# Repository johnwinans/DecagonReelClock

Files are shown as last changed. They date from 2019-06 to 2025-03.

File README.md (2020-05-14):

# DecagonReelClock
Design files for a 3D printed decagon reel clock.  Project files include a 2-part 
decagon reel, drive gear, mounting bracket and printable digits to glue onto the reels.

Inspired by various pinball counter and clock projects like this one:

https://makezine.com/projects/convert-pinball-score-reel-clock/

...and the Gottlieb Decagon Score Reels of the '70s:

https://youtu.be/1tYzWID41jc

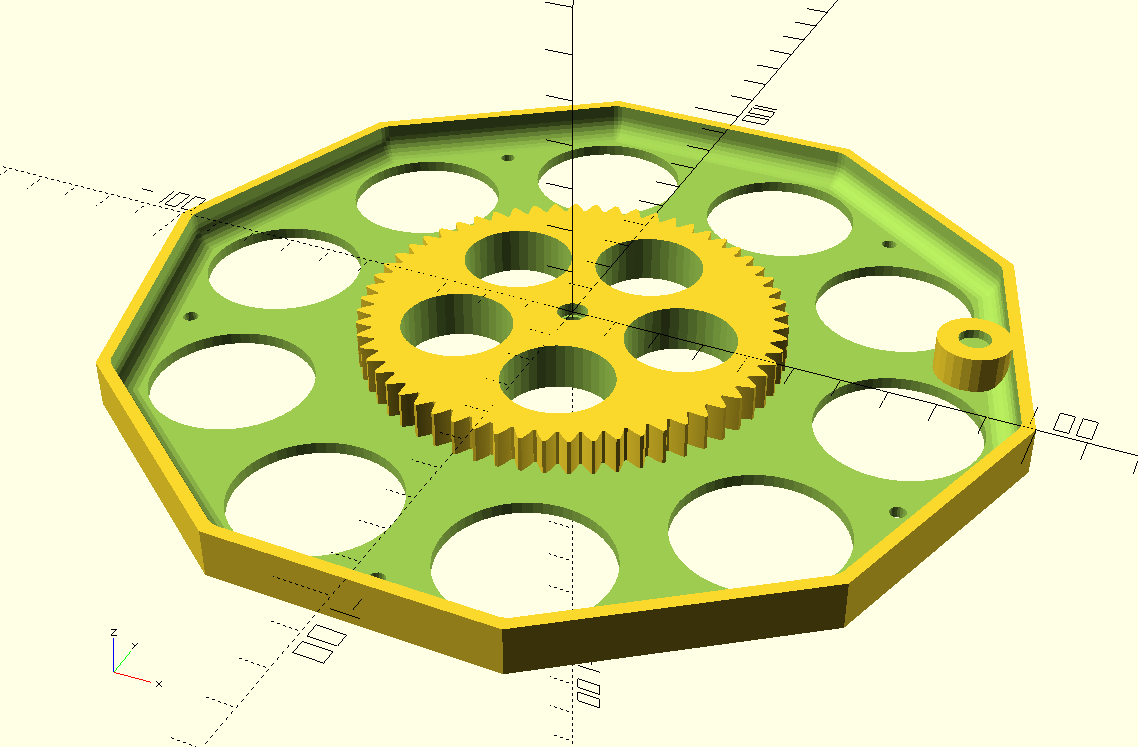
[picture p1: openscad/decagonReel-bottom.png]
Decagon Back


Part suppliers:

* NEMA 17 stepper motors (for 200mm reels) amazon.com ASIN: B07582D2R8
* 28BYJ-48 stepper motors (for 140mm reels) amazon.com ASIN: B00LPK0E5A
* 3mm x 150mm axles amazon.com ASIN: B00JR56KI0
* 3mm bearings amazon.com ASIN: B00ZHSQX42
* Index magnets amazon.com ASIN: B07CPMQJHF
* M3 bolts: asmc.net 0000-102370
* M3 NYLOC nuts: asmc.net 0000-102035
* M3 grub screws amazon.com ASIN: B07792FFJV
* M3 washers amazon.com ASIN: B000FN15YM

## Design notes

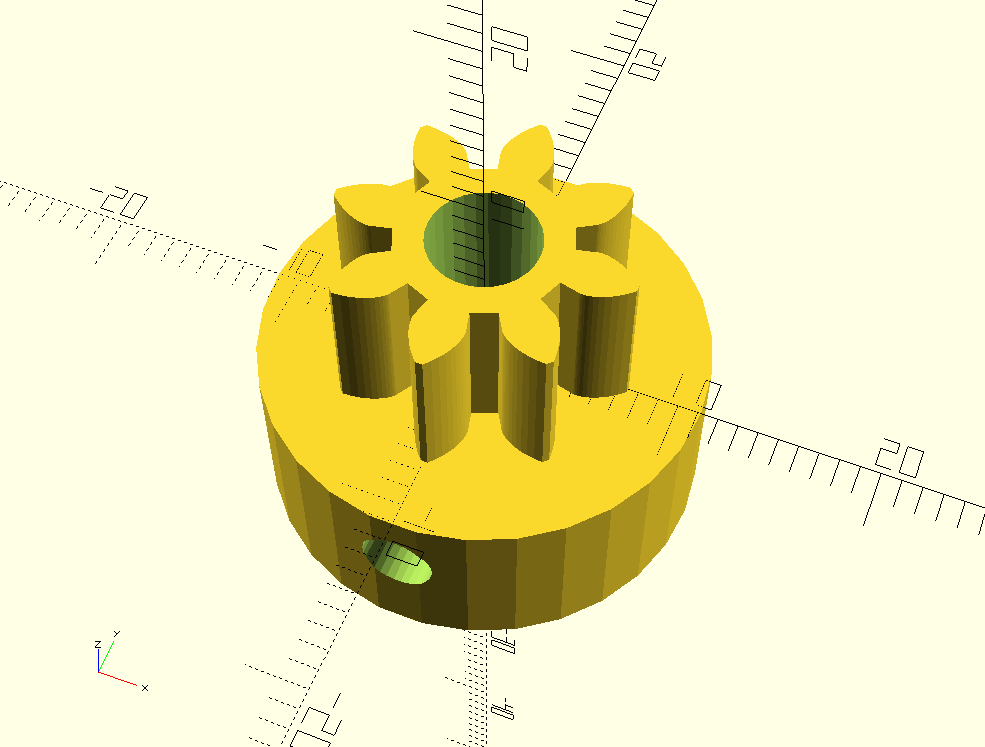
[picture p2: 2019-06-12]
openscad/gear.png

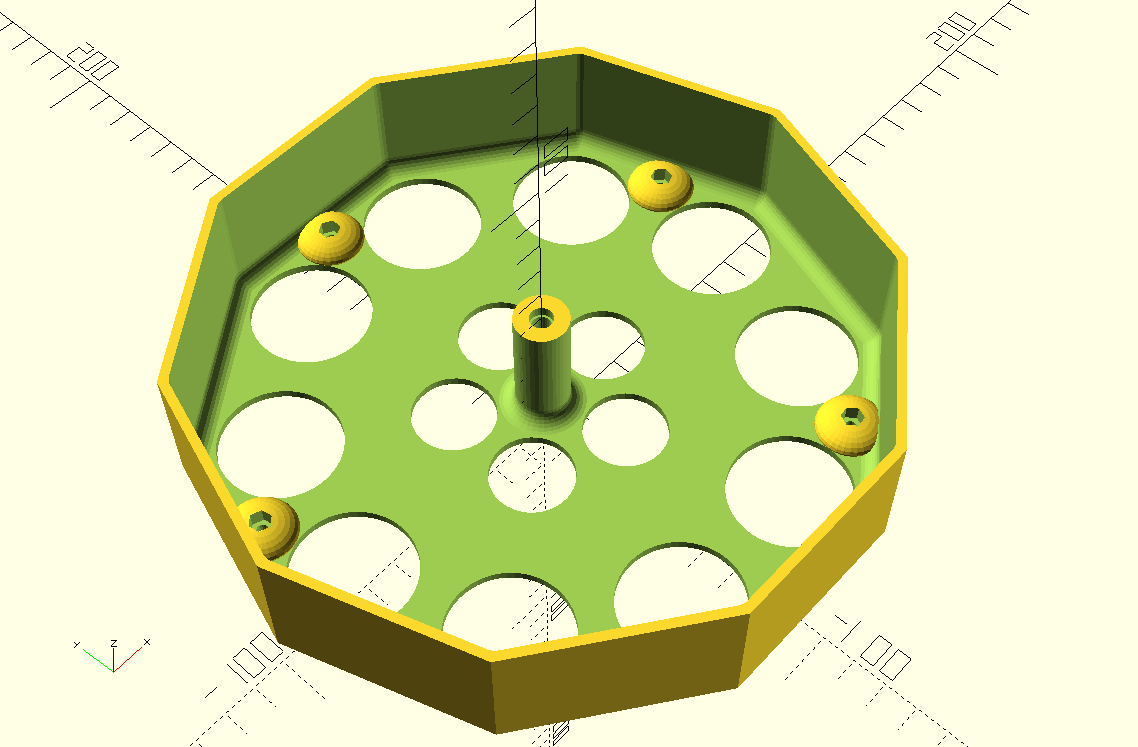
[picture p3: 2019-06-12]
openscad/decagonReel-top.png

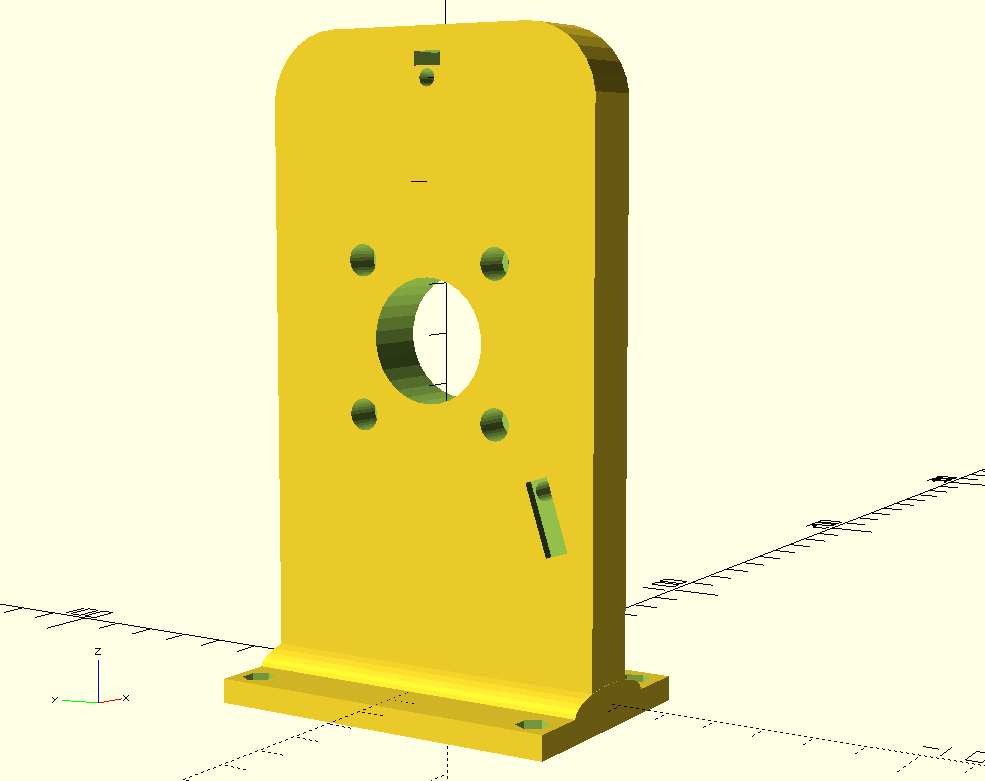
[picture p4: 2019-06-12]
openscad/bracket.png

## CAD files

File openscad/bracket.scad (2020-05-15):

/*
    bracket.scad

    A mounting bracket for a decagon clock reel.

    Copyright (C) 2019  John Winans

    This program is free software: you can redistribute it and/or modify
    it under the terms of the GNU General Public License as published by
    the Free Software Foundation, either version 3 of the License, or
    (at your option) any later version.

    This program is distributed in the hope that it will be useful,
    but WITHOUT ANY WARRANTY; without even the implied warranty of
    MERCHANTABILITY or FITNESS FOR A PARTICULAR PURPOSE.  See the
    GNU General Public License for more details.

    You should have received a copy of the GNU General Public License
    along with this program.  If not, see <https://www.gnu.org/licenses/>.
*/



/*
    Official source and documentation:
        https://github.com/johnwinans/DecagonReelClock
*/



circular_pitch=268;
function pitch_radius(number_of_teeth, circular_pitch) = (number_of_teeth * circular_pitch / 180) / 2;

BearingOD=10.5;
BearingThickness=4;

axleFudge = .1;     // extra space to deal with imperfect gear teeth

// 60 teeth hath the wheel & 8 hath the driver gear for 200mm reels
//axleSpacing = pitch_radius(68, circular_pitch) + axleFudge;
// 32+12 teeth for 140mm reels
axleSpacing = pitch_radius(32+12, circular_pitch) + axleFudge;

echo("axle spacing=", axleSpacing);


mountingBracket();

module mountingBracket()
{
    wheel_thickness = 4;
    
    wallCornerRad = 15;
    wallthickness = 10; // 13=NEMA17, 10=28BYJ-48
    //wallWidth = 75;
    wallWidth = 52;
    wallHeight = 95;   // larger wheel = 130;
    wheel_dia = 140;    // NEMA17 = 200;
    footWidth = 50;
    sensorRadius = wheel_dia/2-wheel_thickness-4;   // NEMA17 = wheel_dia/2-15; 
    
    difference()
    {
        union()
        {
            // the base
            translate([-footWidth/2,-wallWidth/2,-5]) cube([footWidth,wallWidth, 5]);

            // the bracket/wall
            minkowski()
            {
                translate([-wallthickness/2,-(wallWidth-wallCornerRad*2)/2,0]) cube([wallthickness, wallWidth-2*wallCornerRad, wallHeight-wallCornerRad]);
                    
                rotate([0,90,0]) cylinder(r=wallCornerRad, h=.001, center=true);
            }    
            
            // a round foot
            scale([1,1,.3]) rotate([90,0,0]) cylinder(d=wallthickness*2, h=wallWidth, center=true);
        }
            
        // some mounting holes 
        for (x = [-(footWidth/2-5), footWidth/2-5])
            for(y = [-(wallWidth/2-5), wallWidth/2-5])
                translate([x,y,0]) 
                {
                    cylinder(d=3.5, h=40, center=true, $fn=20);
                    translate([0,0,-2.5]) cylinder(d=6.6, h=10, $fn=6);
                }
        
        
        // remove the minkowski noise below the base
        translate([0,0,-5-(wallCornerRad+50)/2]) cube([wallthickness+50, wallWidth+50, wallCornerRad+50], center=true);
    
        // wheel axle hole
        translate([wallthickness/2+.002,0,wallHeight-10]) axleNeg();
        translate([0,0,wallHeight-10]) rotate([90,0,-90]) m3GrubHubNeg(hubZ=wallthickness);
                   
        translate([wallthickness/2+.002,0,wallHeight-10-axleSpacing-axleFudge]) motorNeg();
                
        // access hole for the grub on the motor gear
        translate([0,0,wallHeight-10-axleSpacing-axleFudge]) rotate([90,0,0]) cylinder(d=6, h=100, $fn=20);
            
        // The index sensor hole (2x5 flat package)
        translate([-(wallthickness/2+.002),0,wallHeight-10]) // axle center
            rotate([-360/20,0,0]) 
                translate([0,0,-(sensorRadius)])
                {
                    translate([0,0,0]) cube([4,5,15], center=true);
                    translate([0,0,5]) rotate([0,90,0]) cylinder(d=4, h=40, center=true, $fn=20);
                }

//                rotate([0,-90,0]) cylinder(d=5, h=100, center=false, $fn=30); // index magnet


    }
    translate([wallthickness/2+.002,0,wallHeight-10-axleSpacing-axleFudge]) motorPos();

    // cable retainer
    crd = 6;
    
    translate([wallthickness/2+crd/2, 20, wallHeight-10-axleSpacing-axleFudge]) 
    {
        difference()
        {
            rotate([0,0,-90]) retainer(len=30, rd=crd);
            // if we angle the bottom then we don't need support material
            translate([crd*.9,0,-len/2]) rotate([0,45,0]) cube([crd*2,crd*2,crd*2], center=true);
        }
    }
    translate([0, wallWidth/2+crd/2, 10]) 
    {
        difference()
        {
            retainer(len=wallHeight-25, rd=crd);
            translate([0,crd*.9,-len/2]) rotate([45,0,0]) cube([crd*2,crd*2,crd*2], center=true);
        }
    }
}
  
// A tube for retaining a cable
module retainer(len, rd=8)
{
    th = 1.25;  // wall thickness
    
    translate([0,0,len/2])
    difference()
    {
        cylinder(d=rd+th*2, h=len, center=true, $fn=30);
        cylinder(d=rd, h=len+1, center=true, $fn=30);
        translate([0, rd/2, 0]) cube([2, rd, len+1], center=true);
    }
}



axleDia=3.5;
// the parts that require removing for an axle mount
module axleNeg()
{
    // wheel axle hole
    rotate([0,-90,0]) cylinder(d=axleDia, h=100, center=false, $fn=30);

    // include a set screw
    
    
    // bearing countersink
   // rotate([0,-90,0]) cylinder(d=BearingOD, h=BearingThickness, center=false);
}

grubDia=3.6;
M3SqNutWidth=6;
M3SqNutHt=2.8;

module m3GrubHubNeg(axle=axleDia, hubZ, hubRad=M3SqNutHt*4)
{
    $fn=30;
    od = axle+M3SqNutHt*2+hubRad;
    grubScrewCenter=grubDia/2+1.8;
    nutFudgeZ=0.3;  // extra depth for the nut hole

    // M3 grub screw nut hole (5.5mm square nut)
    // translating to .4 in Y allows as few as 10 teeth on the gear
    translate([-(M3SqNutWidth/2), axle/2+.6, -(M3SqNutWidth/2)-nutFudgeZ]) cube([M3SqNutWidth, M3SqNutHt, hubZ+grubScrewCenter]);

    // M3 grub screw hole
    translate([0, od/2, 0/*grubScrewCenter*/]) rotate([90,0,0]) cylinder(d=grubDia, h=od, center=true);
}


module motorNeg()
{
    //nmea17Neg();
    stepper28byj48Neg();
}

module motorPos()
{
    stepper28byj48Pos();
}

// The positive portion of a 28byj-48 stepper mount
module stepper28byj48Neg()
{
    bracketOffset = 8;          // mounting holes are 8mm offset from center of shaft
    bracketSpacing = 35/2;      // mounting holes spacing is 35mm on center
    
    rotate([0,90,0]) cylinder(d=25, h=100, center=true, $fn=30);

    translate([0,0,-bracketOffset])
    {
        for ( y = [ -bracketSpacing, bracketSpacing ])
        {
            // bolt holes
            translate([0,y,0]) rotate([0,-90,0]) cylinder(d=3.5, h=40, center=true, $fn=20);
            // countersinks
            translate([-5, y, 0]) rotate([0,-90,0])
            cylinder(d=6.6, h=10, $fn=6);
        }
    }
}

// The negative portion of a 28byj-48 stepper mount
module stepper28byj48Pos()
{
    bracketOffset = 8;
    translate([0,0,-bracketOffset]) slottedNotch();
}


// A slotted notch for guiding a 28byj-48 stepper mounting bracket
module slottedNotch()
{
    bracketSpacing = 35/2;      // offset from center to the bracket mounting holes
    bracketWith = 7.3;          // the width of the mounting brackets 
    bracketLength = 42;         // the total outer length of the brackets
    motorHousingDiameter = 29;
    
    difference()
    {
        hull()
        {
            translate([0,bracketSpacing,0]) rotate([0,90,0]) cylinder(d=bracketWith+6, h=2, center=true, $fn=30);
            translate([0,-bracketSpacing,0]) rotate([0,90,0]) cylinder(d=bracketWith+6, h=2, center=true, $fn=30);
        }

        hull()
        {
            translate([0,bracketSpacing,0]) rotate([0,90,0]) cylinder(d=bracketWith, h=3, center=true, $fn=30);
            translate([0,-bracketSpacing,0]) rotate([0,90,0]) cylinder(d=bracketWith, h=3, center=true, $fn=30);
        }
        cube([10,motorHousingDiameter,bracketWith+10], center=true);
    }
}

// the parts that require cutting away to mount a nema17 motor
module nmea17Neg()
{
    // the motor shaft hole
    rotate([0,90,0]) cylinder(d=25, h=100, center=true, $fn=30);
    
    // frame-mounting holes
    for (z = [ 31/2, -31/2 ])
        for (y = [ 31/2, -31/2 ])
        {
            // M3 bolt holes
            translate([0, y, z]) rotate([0,-90,0]) cylinder(d=3.8, h=100, center=false, $fn=30);
            // countersinks
            translate([-5, y, z]) rotate([0,-90,0]) cylinder(d=6.5, h=100, center=false, $fn=30);
        }
}

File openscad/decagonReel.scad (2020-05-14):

/*
    clock_reel.scad

    A decagon reel suitable for displaying digits.  (A large 
    reel like those used on electromechanical pinball games.)

    Copyright (C) 2019  John Winans

    This program is free software: you can redistribute it and/or modify
    it under the terms of the GNU General Public License as published by
    the Free Software Foundation, either version 3 of the License, or
    (at your option) any later version.

    This program is distributed in the hope that it will be useful,
    but WITHOUT ANY WARRANTY; without even the implied warranty of
    MERCHANTABILITY or FITNESS FOR A PARTICULAR PURPOSE.  See the
    GNU General Public License for more details.

    You should have received a copy of the GNU General Public License
    along with this program.  If not, see <https://www.gnu.org/licenses/>.
*/



/*
    Official source and documentation:
        https://github.com/johnwinans/DecagonReelClock
        
    Select to print the entire reel or just the top or bottom in the code below.
    By default, nothing is rendered because it can take over a minute.
*/




use <MCAD/involute_gears.scad>

$fa=2;    // render high quality for printing (takes a minute to compile!)

m3nutDia=6.6;       // The diameter of the hex point-to-point on an M3 nut
m3BoltDia=3.4;      // the diameter of an M3 bolt shaft hole

// outer diameter of the reel
wheel_dia=140;    // 140mm decagon for 140mm print beds
//wheel_dia=200;      // bigger decagon for larger print beds (like TAZ)

wheel_height=wheel_dia/4;    // how wide the reel will be (or the height when printing it sideways)
wheel_thickness=4;  // how thick the reel hub should be

wheel_axle_bore_diameter=5.4;  // the size of the hole in the hub (for the axle)


wheel_axle_bearing_diameter=6.4;
bearing_height=3;

facetHeight = cos(((10-2)*180)/10/2)*(wheel_dia/2)*2;
echo("wheel_height=", wheel_height, "facet=", facetHeight);

//reel();                         // <---------------  Render the entire reel

//rotate([180,0,0]) reelBottom(); // <--------------- Render the bottom only

reelTop();                      // <--------------- Render the top only




//testBearingCountersink();
module testBearingCountersink()
{
    difference()
    {
        cylinder(d=15, h=10, $fn=30);
        translate([0,0,10-bearing_height+.001]) cylinder(d=wheel_axle_bearing_diameter, h=bearing_height, $fn=30);
        translate([0,0,-.5]) cylinder(d=wheel_axle_bore_diameter, h=wheel_height+1, $fn=30);   
    }
}

/**
* A 'blob' with a hexagonal hole suitable for holding an M3 nyloc
* nut.
***********************************************************************/
module nutRetainer(boltDia, nutDia)
{
    difference()
    {
        union()
        {
            translate([0,0,-2.5]) cube([20,20,5], center=true);
            scale([1,1,.5]) sphere(r=10);
        }
        cylinder(d=nutDia, h=10, $fn=6);
        translate([0,0,-5.1]) cylinder(d=boltDia, h=20, $fn=20);
    }
}


/**
* Render just the top half of the reel (better suited to 3D printing
* with no supports.)
***********************************************************************/
module reelTop()
{
    difference()
    {
        reel();
        translate([-100,-100,0]) cube([200,200,8+2.5]);
    }
}

/**
* Render just the bottom half of the reel (better suited to 3D printing
* with no supports.)
***********************************************************************/
module reelBottom()
{
    difference()
    {
        reel();
        translate([-100,-100,8+2.5]) cube([200,200,100]);
    }
}

/**
* The decagon score reel.
***********************************************************************/
module reel()
{
    // gearTeeth=60;
    gearTeeth=32;
    
    // how far from the center to drill the bolt holes
    boltRad=wheel_dia/2-wheel_thickness-4;
    
    difference()
    {
        union()
        {
            wheel();
    
            // 60 teeth = 6 teeth/digit
            mygear($fn=20,
                number_of_teeth=gearTeeth, 
                bore_diameter=wheel_axle_bore_diameter,
                hub_thickness=0,
                rim_thickness = 8,      // how thick the 'tire' of the gear will be
                gear_thickness = 8      // how thick the inner-wheel will be
                );
            
            // add some material that we can hollow out to use for nut-holders
            for ( t = [ 0 : 72 : 360 ] )
                rotate([0,0,t]) translate([boltRad,0,8+5]) 
                    cylinder(d=m3BoltDia+8, h=5);
        }
        
        // index magnet mounting hole
        if(false)
            rotate([0,0,-360/10]) translate([pitch_radius(gearTeeth)-6,0,-.001]) cylinder(d=7, h=2.1, $fn=20);


        // put relief holes around the hub (if it is big enough)
        for ( t = [ 18 : 36 : 360 ] )
            rotate([0,0,t]) translate([wheel_dia/3,0,0]) cylinder(d=wheel_dia/6, h=100, $fn=30);

        // hollow out the gear
        for ( t = [ 0 : 72 : 360 ] )
            rotate([0,0,t]) translate([pitch_radius(gearTeeth)*.57,0,-.1]) cylinder(d=pitch_radius(gearTeeth)/2, h=100, $fn=30);        
        
        // some bolt holes to attach the top & bottom together 
        for ( t = [ 0 : 72 : 360 ] )

            rotate([0,0,t]) translate([boltRad,0,0]) 
            {
                cylinder(d=m3BoltDia, h=100, $fn=20);   // the bolt hole
                cylinder(d=m3BoltDia+4, h=8, $fn=20);   // head countersink
                translate([0,0,8+5]) cylinder(d=m3nutDia, h=100, $fn=6);    // nut countersink
            }
            
        // axle bearings
        translate([0,0,-.001]) cylinder(d=wheel_axle_bearing_diameter, h=bearing_height, $fn=30);
        translate([0,0,wheel_height-bearing_height+.001]) cylinder(d=wheel_axle_bearing_diameter, h=bearing_height, $fn=30);

    }
    
    // index magnet mounting hole
    difference()
    {
        rotate([0,0,-360/10]) translate([boltRad,0,0]) cylinder(d=m3BoltDia+8, h=8, $fn=20);
        rotate([0,0,-360/10]) translate([boltRad,0,-.001]) cylinder(d=7, h=2.1, $fn=20);
    }
}


/**
* A hollowed out decagon.
***********************************************************************/
module wheel()
{
    wheel_inner_dia=wheel_dia-2*wheel_thickness;

    difference()
    {
        cylinder(d=wheel_dia, h=wheel_height, $fn=10);

        // hollow out the top
        translate([0,0,5+5+8]) 
            minkowski()
            {
                difference()
                {
                    cylinder(d=wheel_inner_dia-10, h=wheel_height+1, $fn=10);       // hollow decagon
                    cylinder(d=wheel_axle_bore_diameter+10+10, h=wheel_height+20); // axle hub
                }
                sphere(r=5,$fn=30);     // fillet all of the corners
            }
            
        // hollow out the bottom
        minkowski()
        {
            cylinder(d=wheel_inner_dia-10, h=8-5, $fn=10);
            sphere(r=5,$fn=30);
        }
        
        // the axle bore
        translate([0,0,-.5]) cylinder(d=wheel_axle_bore_diameter, h=wheel_height+1, $fn=30);   
    }
}



/**
* A wrapper for rendering a gear.
***********************************************************************/
circular_pitch=268;

module mygear(
    number_of_teeth = 48,
    gear_thickness = 5,
    rim_thickness = 7,
    rim_width = 3,
    hub_thickness = 10,
    hub_diameter = 10,
    bore_diameter = 6)
{
    gear (number_of_teeth=number_of_teeth,
        circular_pitch=circular_pitch,
        gear_thickness = gear_thickness,
        rim_thickness = rim_thickness,
        rim_width = rim_width,
        hub_thickness = hub_thickness,
        hub_diameter = hub_diameter,
        bore_diameter = bore_diameter,
        circles=0,
        twist = 0,
        involute_facets = 12,
        circle_facets = 7);    
}

function pitch_radius(number_of_teeth, circular_pitch=circular_pitch) = (number_of_teeth * circular_pitch / 180) / 2;

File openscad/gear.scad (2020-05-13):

/*
    gear.scad

	A drive gear for NEMA17 motor.

    Copyright (C) 2019  John Winans

    This program is free software: you can redistribute it and/or modify
    it under the terms of the GNU General Public License as published by
    the Free Software Foundation, either version 3 of the License, or
    (at your option) any later version. 

    This program is distributed in the hope that it will be useful,
    but WITHOUT ANY WARRANTY; without even the implied warranty of
    MERCHANTABILITY or FITNESS FOR A PARTICULAR PURPOSE.  See the
    GNU General Public License for more details.

    You should have received a copy of the GNU General Public License
    along with this program.  If not, see <https://www.gnu.org/licenses/>.
*/
    
    
    
/*  
    Official source and documentation:
        https://github.com/johnwinans/DecagonReelClock
*/


use <MCAD/involute_gears.scad>

m5bore=5.6;
m3bore=3.4;
m3nbore=6.5;        // countersink diameter for an M3 hex nut

$fs=2;
bore_countersink_dia=9.5;       // head countersink diameter for an M5 bolt head
bore_countersink_depth=5+1;     // countersink depth for an M5 bolt head
bore_diameter=m5bore;           // axle diameter for loose fit on an M5 bolt

nema17shaft=5.5;

involute_facets=12;	
circle_facets=7;
circular_pitch=268;

meshFudge=.15;   // extra space between gear axles


small(nema17shaft, teeth=12);
//small(m3bore, teeth=26);
//small(m3bore, teeth=16);

//m3GrubHub(nema17shaft, 9);

module small(bore=10, teeth=10)
{
    hubZ=9;
	difference()
    {
        union()
        {
        translate([0,0,-hubZ]) m3GrubHubPos(bore, hubZ, $fn=30);
		gear (number_of_teeth=teeth,
			circular_pitch=268,
			gear_thickness = 8,
			rim_thickness = 8,
			hub_thickness = 0,
			hub_diameter = 20,
			bore_diameter = 0,
			circles=0,
			twist = 0,
			involute_facets = involute_facets,
			$fn=30);
        }
        translate([0,0,-hubZ]) m3GrubHubNeg(bore, hubZ, axleZ=hubZ+8+.1, $fn=30);
	}
}

//******************************************************************************
grubDia=3.6;
M3SqNutWidth=6;
M3SqNutHt=2.8;

// This is the definition of the axle shaft hole
module axleHoleNeg(bore, h)
{
    // A hole with flats, suitable for 28BYJ-48
    //translate([0,0,h/2])
    intersection()
    {
        cylinder(d=bore, h=h);
        translate([-bore/2, -3.1/2, 0]) cube([bore,3.1,h+.001]);
    }
    // clear some space for the non-flattened base of the shaft
    cylinder(d=bore, h=1.5);
}


module m3GrubHubPos(axle, hubZ)
{
    od = axle+M3SqNutHt*6;
    cylinder(d=od, h=hubZ, $fn=40);
}

module m3GrubHubNeg(axle, hubZ, axleZ, hubRad=M3SqNutHt*4)
{
    $fn=30;
    od = axle+M3SqNutHt*6;
    grubScrewCenter=hubZ/2;

    nutFudgeZ=0.5;  // extra depth for the nut hole
    
    // shaft hole
    translate([0,0,-.001]) axleHoleNeg(bore=axle, h=axleZ);
    
    // M3 grub screw nut hole (5.5mm square nut)
    // translating to .4 in Y allows as few as 10 teeth on the gear
    //nutAxleGap=.01;
    nutAxleGap=.8;
    translate([-(M3SqNutWidth/2), axle/2+nutAxleGap, -.001]) cube([M3SqNutWidth, M3SqNutHt, grubScrewCenter+M3SqNutWidth/2+nutFudgeZ]);  //M3SqNutWidth+nutFudgeZ]);
    
    // M3 grub screw hole
    translate([0, 0, grubScrewCenter]) rotate([-90,0,0]) cylinder(d=grubDia, h=od/2);//, center=true);
}

module m3GrubHub(axle, hubZ=10)
{
    difference()
    {
        m3GrubHubPos(axle, hubZ);
        m3GrubHubNeg(axle, hubZ);
    }
}

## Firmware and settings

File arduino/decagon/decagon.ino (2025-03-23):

#if 1

// (c) Michael Schoeffler 2017, http://www.mschoeffler.de
#include <Stepper.h>
#define STEPS 2038 // the number of steps in one revolution of your motor (28BYJ-48)
Stepper stepper(STEPS, 8, 10, 9, 11);
void setup() {
  // nothing to do
}
void loop() {
//      stepper.setSpeed(1); // 1 rpm
//      stepper.step(2038); // do 2038 steps -- corresponds to one revolution in one minute

  powerOff();
  delay(1000); // wait for one second
  stepper.setSpeed(10); // rpm
  stepper.step(-2048); // do 2038 steps in the other direction with faster speed 
}

// whaddaya say we shut off the motor when we are not using it?
void powerOff()
{
  digitalWrite(8, LOW);
  digitalWrite(9, LOW);
  digitalWrite(10, LOW);
  digitalWrite(11, LOW);
}


#else




#define IN1 8
#define IN2 9
#define IN3 10
#define IN4 11
int Steps = 0;
boolean Direction = true;


//#define DLY 800
#define DLY 800


void setup() 
{
  Serial.begin(9600);
  pinMode(IN1, OUTPUT);
  pinMode(IN2, OUTPUT);
  pinMode(IN3, OUTPUT);
  pinMode(IN4, OUTPUT);
}
void loop() {
  for(int i=0; i<4096; i++)
  {
    stepper(1);
    delayMicroseconds(DLY);
  }
  //Direction = !Direction;
  delay(1000);
}

void stepper(int xw) 
{
  for (int x = 0; x < xw; x++) 
  {
    switch (Steps) 
    {
    case 0:
    digitalWrite(IN1, LOW);
    digitalWrite(IN2, LOW);
    digitalWrite(IN3, LOW);
    digitalWrite(IN4, HIGH);
    break;
    case 1:
    digitalWrite(IN1, LOW);
    digitalWrite(IN2, LOW);
    digitalWrite(IN3, HIGH);
    digitalWrite(IN4, HIGH);
    break;
    case 2:
    digitalWrite(IN1, LOW);
    digitalWrite(IN2, LOW);
    digitalWrite(IN3, HIGH);
    digitalWrite(IN4, LOW);
    break;
    case 3:
    digitalWrite(IN1, LOW);
    digitalWrite(IN2, HIGH);
    digitalWrite(IN3, HIGH);
    digitalWrite(IN4, LOW);
    break;
    case 4:
    digitalWrite(IN1, LOW);
    digitalWrite(IN2, HIGH);
    digitalWrite(IN3, LOW);
    digitalWrite(IN4, LOW);
    break;
    case 5:
    digitalWrite(IN1, HIGH);
    digitalWrite(IN2, HIGH);
    digitalWrite(IN3, LOW);
    digitalWrite(IN4, LOW);
    break;
    case 6:
    digitalWrite(IN1, HIGH);
    digitalWrite(IN2, LOW);
    digitalWrite(IN3, LOW);
    digitalWrite(IN4, LOW);
    break;
    case 7:
    digitalWrite(IN1, HIGH);
    digitalWrite(IN2, LOW);
    digitalWrite(IN3, LOW);
    digitalWrite(IN4, HIGH);
    break;
    default:
    digitalWrite(IN1, LOW);
    digitalWrite(IN2, LOW);
    digitalWrite(IN3, LOW);
    digitalWrite(IN4, LOW);
    break;
    }
  
    SetDirection();
  }
}

  
void SetDirection() 
{
  if (Direction == 1) 
  {
    Steps++;
  }
  if (Direction == 0) 
  {
    Steps--;
  }
  if (Steps > 7) 
  {
    Steps = 0;
  }
  if (Steps < 0) 
  {
    Steps = 7;
  }
} 

#endif

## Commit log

2019-06-09 First draft of the decagon reel.
    [decagonReel.scad]
2019-06-12 Add countersinks for bearings.
    [decagonReel.scad]
2019-06-12 Added bracket & drive gear.
    [bracket.scad, gear.scad]
2019-06-12 Added printable digits for the reel.
2019-06-12 Added rendered stl files for everything.
    [bracket.stl, decagonReel-bottom.stl, decagonReel-top.stl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]
2019-06-12 Remove debug marker.
    [bracket.scad]
2019-06-12 Added images of the stl files.
2019-06-12 Reduce the bearing countersink diameter by .1mm.
    [decagonReel-bottom.stl, decagonReel-top.stl, decagonReel.scad]
2020-05-13 New gear & brackets to reduce mesh play.
    [bracket.scad, bracket.stl, decagonReel-bottom.stl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]
2020-05-13 Change bracket height to better fit 140mm reel
    [bracket.scad]
2020-05-14 Spell axle correctly ;-)
    [decagonReel.scad]
2020-05-14 Add ASIN for 28BYJ-48 steppers for 140mm reels
2020-05-15 Optimize bracket for 140mm reel.
    [bracket.scad]
2020-05-15 2+2=4, add nut-retainers, tweak cable guides.
    [bracket.scad]
